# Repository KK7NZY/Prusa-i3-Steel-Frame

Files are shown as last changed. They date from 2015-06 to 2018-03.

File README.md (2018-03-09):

P3Steel
---
RepRap P3Steel parts and build instructions.

### Bill of Materials

**Vitamins**

- (1) [Steel Frame V2.01](http://orballoprinting.com/en/frame/8-prusa-i3-steel-frame-p3steel.html)
- (1) [Steel X-Carriage Kit](https://www.ebay.com/itm/P3Steel-Lasercut-All-metal-kit-for-v2-v2-5-v4-Frame-Prusa-i3-3D-Printer-RepRap/142481311508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)

**Proteins**

- (2) psu-clamp-top.stl
- (2) psu-clip.stl
- (1) psu-clamp-bottom.stl
- (2) endstop-holder.stl
- (1) feet-dampner-set.stl
- (1) y-belt-holder.stl
- (1) y-endstop.stl
- (1) ir-sensor-mount.stl

**Electronics**

- (1) [Azteeg X5 mini v1.1](https://www.panucatt.com/azteeg_X5_mini_reprap_3d_printer_controller_p/ax5mini.htm)
- (1) 12v/30a DC Universal Regulated Switching Power Supply 360w
- (1) 9 ft. 14/3 Power Tool Replacement Cord
- (1) [All-metal E3D v6 Hotend - 12 Volt / 1.75mm Universal](https://www.filastruder.com/products/all-metal-e3d-v6-hotend)
- (1) 12V 220W Silicone Heater w/adhesive tape (200mm x 200mm)
- (1) [Mini Differential IR Height Sensor](https://www.filastruder.com/collections/electronics/products/mini-differential-ir-height-sensor)

**Hardware**

- (2) 8mm x 320mm Precision Chromed Linear Shaft Rod
- (2) 300mm x 8mm Lead 4 Start Lead Screw & Nut
- (2) 8mm x 406mm Precision Chromed Linear Shaft Rod
- (4) Heated Bed Adjustment M3 Thumb Nut
- (1) MK8 Filament all-Metal Remote Bowden Extruder Parts
- (1) Aluminum Spacer (6 x 1/4" x 3/8")
- (3) Mechanical Endstop Switch
- (1) Aluminum Bed Build Plate (200mm x 200mm x 2mm)
- (1) Heated Bed Tempered Borosilicate Glass Plate

**Mechanical parts**

- (4) LM8UU Linear Bearings 
- (7) Igus DryLin® RJ4JP 01-08
- (2) 5mm to 8mm Shaft Rigid Motor Wheel Coupling Coupler 
- (1) GT2 2mm pitch 6mm wide Timing Belt (5 Meters)
- (2) GT2 Pulley 16T 6mm Width
- (2) 608 Ball Bearing
- (4) [NEMA 17 Stepper Motor](https://www.lulzbot.com/store/parts/nema-17-stepper-motor)
- (1) [Half Height NEMA 17 Stepper Motor](https://www.lulzbot.com/store/parts/half-height-nema-17-stepper-motor)
- (30) [Female Crimp terminal for 0.1" pitch headers](https://mod-one.com/female-crimp-terminal-for-0-1-pitch-headers-5-pack/)
- (5) Dupont 2.54mm Connector Housing Female

**Optional**

- (1) [Mellow-Yellow MDPC-X Sleeve (25ft)](https://mod-one.com/mdpc-x-cable-sleeve/)

### Temperature Control

http://smoothieware.org/temperaturecontrol?s[]=temperaturecontrol&s[]=pid&s[]=autotuning#pid-autotuning

**PID Settings**

```sh
# E3D-v6 Hotend
M303 E0 S230 C10
// Cycle 4: max 236.676,min:225.84,avg seperation: 0.281876
   Ku: 59.9243,Pu 35.25
   Kp: 36.0
   Ki: 2.040
   Kd: 158

# Heatbed
M303 E1 S50 C8
// Cycle 4: max: 50.6263, min: 49.3329, avg separation: 0.00749207
   Ku: 502.053, Pu: 52.1
   Trying:
   Kp: 301.2
   Ki: 11.564
   Kd:  1962
```

### Resources:
- [P3Steel Wiki](http://reprap.org/wiki/P3Steel)
- [Triffid Hunter's Calibration Guide](http://reprap.org/wiki/Triffid_Hunter's_Calibration_Guide)
- [Prusa Calculator](http://www.prusaprinters.org/calculator/)
- [Prusa3D Slic3r](https://github.com/prusa3d/Slic3r)
- [RepRap GCode Cheat Sheet](https://thingiverse-production-new.s3.amazonaws.com/assets/87/b0/2c/f5/4c/CheatSheet.pdf)
- [Mini height sensor board](https://miscsolutions.wordpress.com/mini-height-sensor-board/)
- [Smoothie Firmware](https://github.com/Smoothieware/Smoothieware/tree/edge/FirmwareBin)
- [E3D-v6_Assembly](https://wiki.e3d-online.com/wiki/E3D-v6_Assembly)
- [Smoothieware Z-probe](http://smoothieware.org/zprobe#configuration-options4)

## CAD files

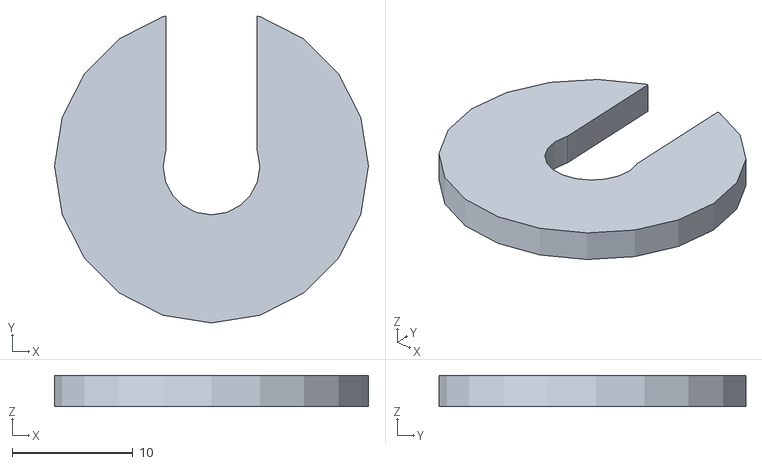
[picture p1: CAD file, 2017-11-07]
proteins/608-bar-spacer.stl
26.0 x 25.4 x 2.60

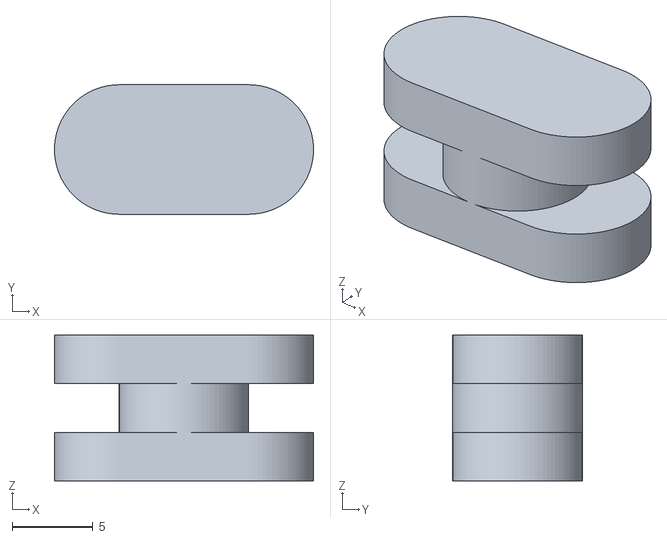
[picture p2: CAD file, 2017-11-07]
proteins/psu-clip.stl
16.0 x 8.00 x 9.00

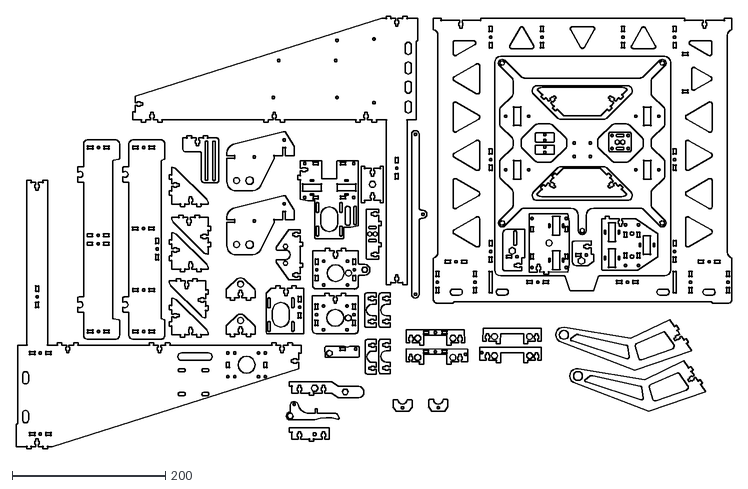
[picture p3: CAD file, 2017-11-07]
vitamins/frame/V1.2-cordobesa-remix/CORDOBESA.dxf
935.1 x 565.2

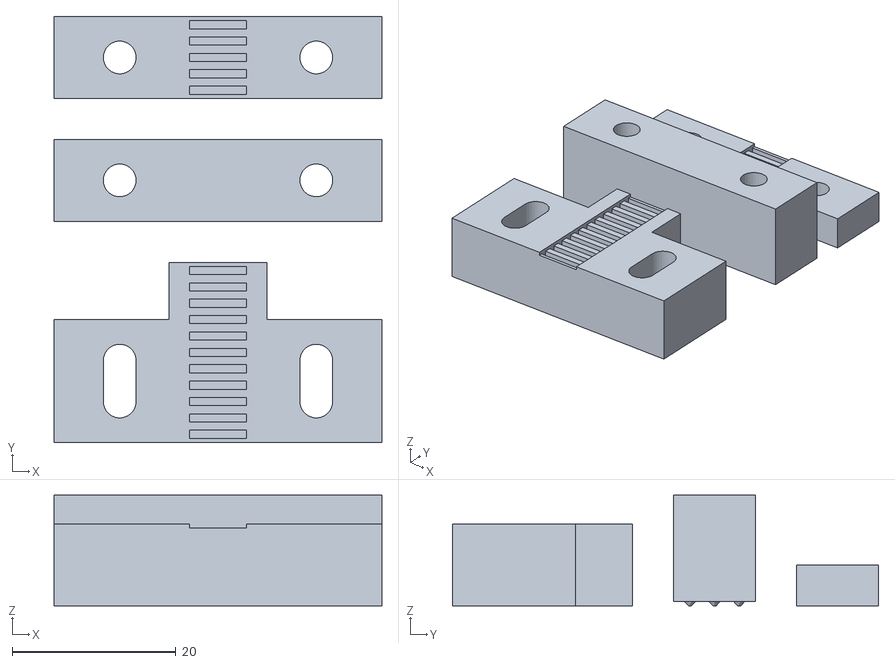
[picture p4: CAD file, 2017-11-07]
proteins/y-belt-holder.stl
40.0 x 52.0 x 13.5

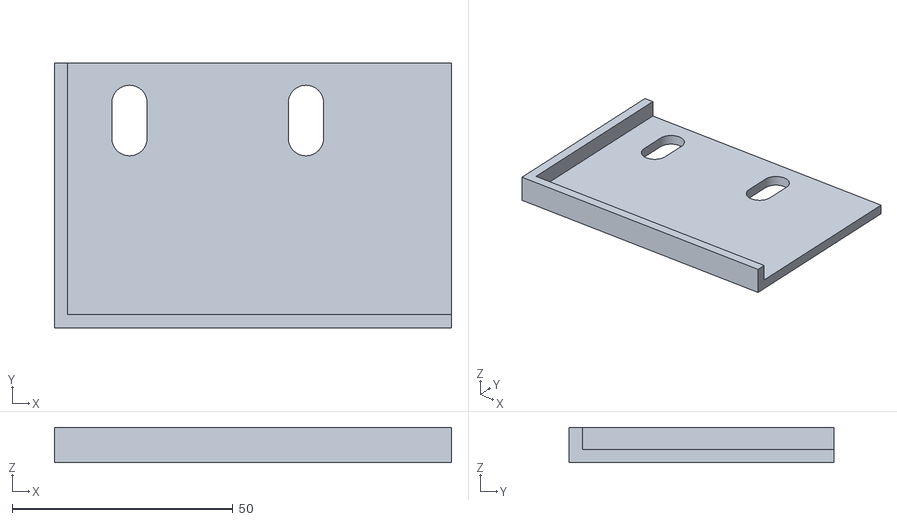
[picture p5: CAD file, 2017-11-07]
proteins/psu-clamp-bottom.stl
90.0 x 60.0 x 8.00

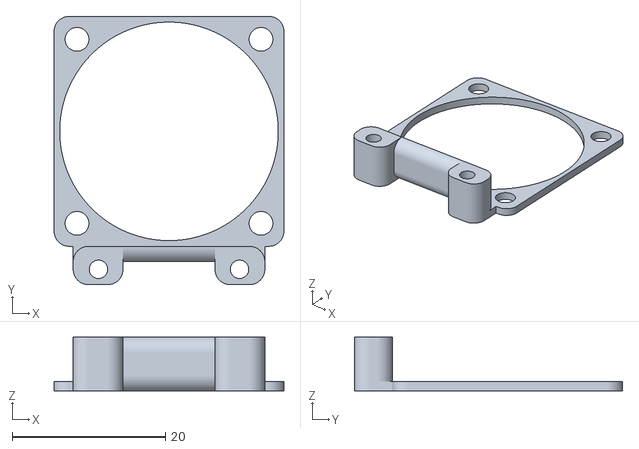
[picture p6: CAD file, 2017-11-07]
proteins/ir-sensor-mount.stl
30.0 x 35.0 x 7.00

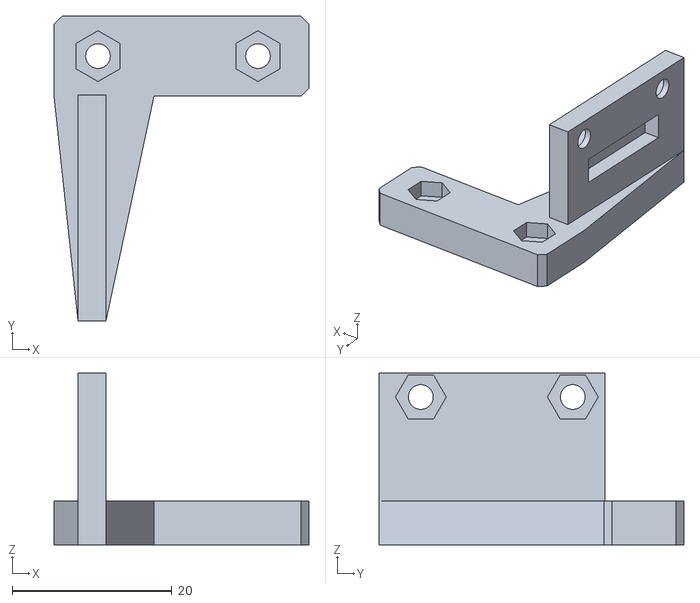
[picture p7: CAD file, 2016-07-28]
proteins/y-endstop.stl
31.9 x 38.1 x 21.5

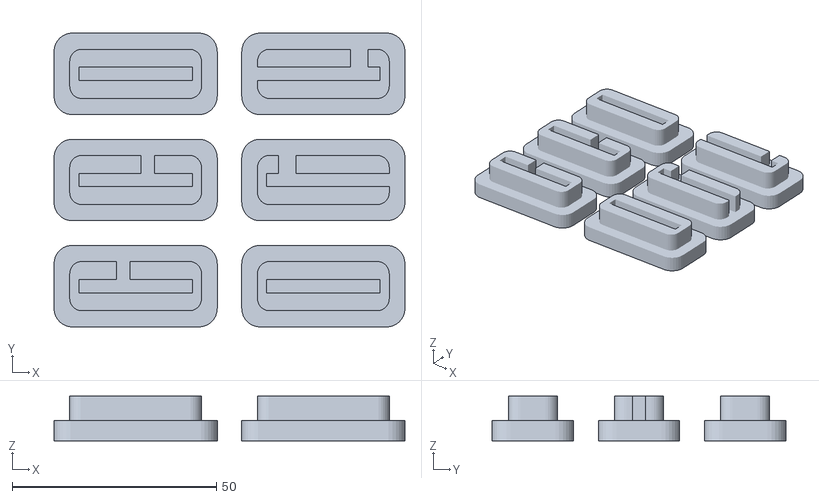
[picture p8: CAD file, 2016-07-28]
proteins/feet-dampner-set.stl
86.0 x 72.0 x 11.0

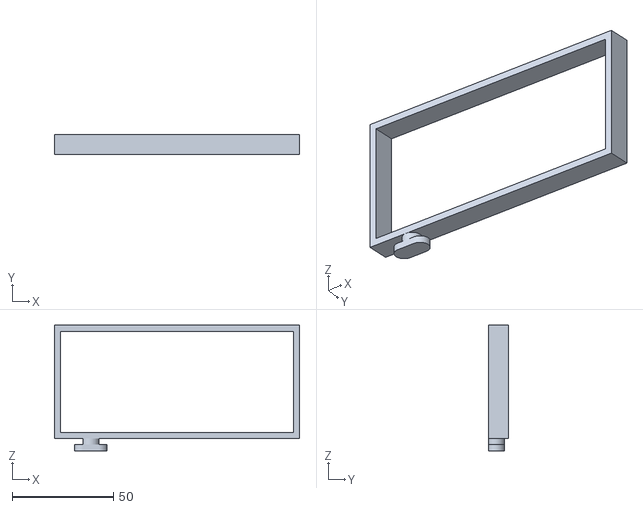
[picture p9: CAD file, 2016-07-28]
proteins/psu-clamp-top.stl
121.0 x 10.00 x 62.0

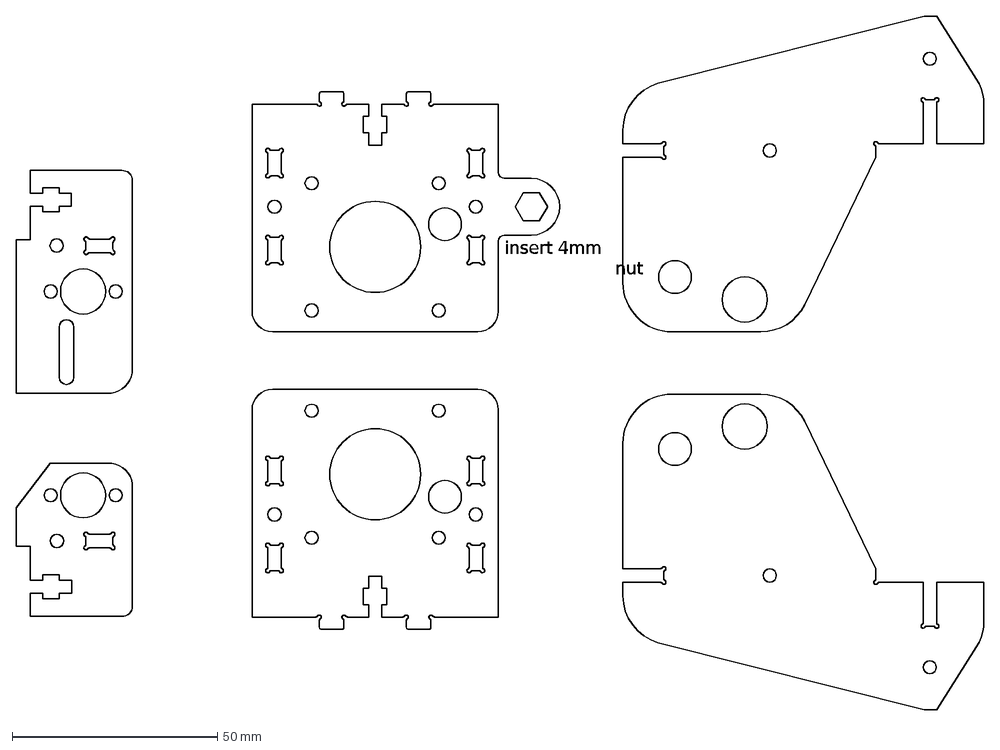
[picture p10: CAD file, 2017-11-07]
vitamins/frame/V1.2-cordobesa-remix/Lead_screw_replacement_parts.dxf
insert 4mm nut

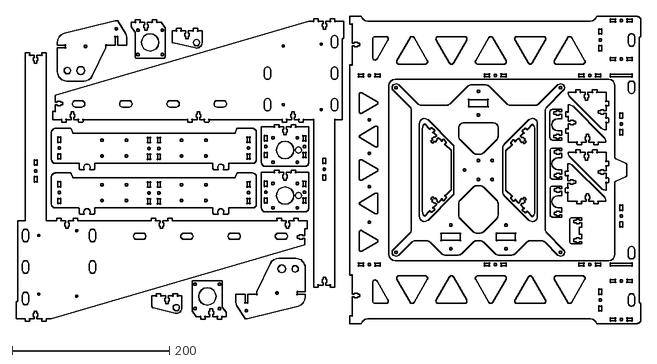
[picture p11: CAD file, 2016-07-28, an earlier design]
vitamins/frame/V1.2/PRUSA_i3_steel_3mm_lasercut_1.2_irobri.dxf
793.6 x 390.0

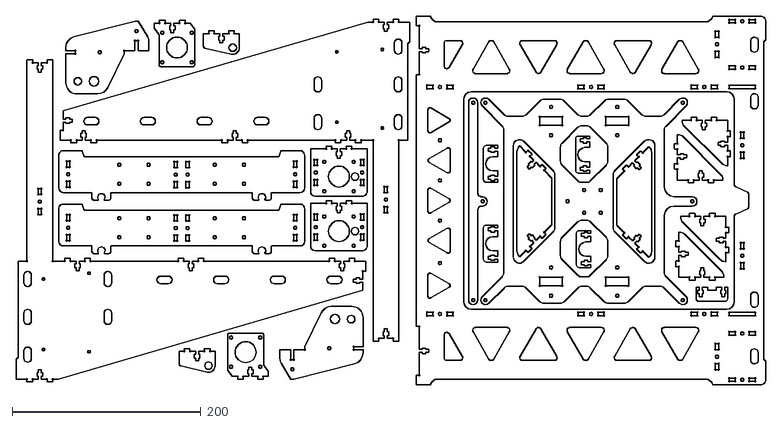
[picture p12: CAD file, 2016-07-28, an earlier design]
vitamins/frame/V2.0/PRUSA_i3_steel_3mm_lasercut_2.0_irobri.dxf
793.6 x 390.0

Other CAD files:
vitamins/frame/V2.5/PRUSA_i3_steel_3mm_lasercut_2.5DXL_e_irobri_V2.dwg
vitamins/frame/V2.1/PRUSA_i3_steel_3mm_lasercut_2.01d_irobri.dwg
vitamins/frame/V1.2-cordobesa-remix/Lead_screw_replacement_parts.dwg
vitamins/frame/V1.2/PRUSA_i3_steel_3mm_lasercut_1.2_irobri.dwg
vitamins/frame/V2.0/PRUSA_i3_steel_3mm_lasercut_2.0_irobri.dwg

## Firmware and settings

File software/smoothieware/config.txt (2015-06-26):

# Robot module configurations : general handling of movement G-codes and slicing into moves
default_feed_rate                            4000             # Default rate ( mm/minute ) for G1/G2/G3 moves
default_seek_rate                            4000             # Default rate ( mm/minute ) for G0 moves
mm_per_arc_segment                           0.5              # Arcs are cut into segments ( lines ), this is the length for these segments.  Smaller values mean more resolution, higher values mean faster computation
#mm_per_line_segment                          5                # Lines can be cut into segments ( not usefull with cartesian coordinates robots ).

# Arm solution configuration : Cartesian robot. Translates mm positions into stepper positions
alpha_steps_per_mm                           80               # Steps per mm for alpha stepper
beta_steps_per_mm                            80               # Steps per mm for beta stepper
gamma_steps_per_mm                           1637.7953        # Steps per mm for gamma stepper

# Planner module configuration : Look-ahead and acceleration configuration
planner_queue_size                           32               # DO NOT CHANGE THIS UNLESS YOU KNOW EXACTLY WHAT YOUR ARE DOING
acceleration                                 3000             # Acceleration in mm/second/second.
#z_acceleration                              500              # Acceleration for Z only moves in mm/s^2, 0 disables it, disabled by default. DO NOT SET ON A DELTA
acceleration_ticks_per_second                1000             # Number of times per second the speed is updated
junction_deviation                           0.05             # Similar to the old "max_jerk", in millimeters, see : https://github.com/grbl/grbl/blob/master/planner.c#L409
                                                              # and https://github.com/grbl/grbl/wiki/Configuring-Grbl-v0.8 . Lower values mean being more careful, higher values means being faster and have more jerk

# Stepper module configuration
microseconds_per_step_pulse                  1                # Duration of step pulses to stepper drivers, in microseconds
base_stepping_frequency                      100000           # Base frequency for stepping

# Stepper module pins ( ports, and pin numbers, appending "!" to the number will invert a pin )
alpha_step_pin                               2.1              # Pin for alpha stepper step signal
alpha_dir_pin                                0.11             # Pin for alpha stepper direction
alpha_en_pin                                 0.10             # Pin for alpha enable pin
alpha_current                                1.0              # X stepper motor current
x_axis_max_speed                             30000            # mm/min
alpha_max_rate                               30000.0          # mm/min actuator max speed

beta_step_pin                                2.2              # Pin for beta stepper step signal
beta_dir_pin                                 0.20             # Pin for beta stepper direction
beta_en_pin                                  0.19             # Pin for beta enable
beta_current                                 1.0              # Y stepper motor current
y_axis_max_speed                             30000            # mm/min
beta_max_rate                                30000.0          # mm/min actuator max speed

gamma_step_pin                               2.3              # Pin for gamma stepper step signal
gamma_dir_pin                                0.22             # Pin for gamma stepper direction
gamma_en_pin                                 0.21             # Pin for gamma enable
gamma_current                                1.0              # Z stepper motor current
z_axis_max_speed                             300              # mm/min
gamma_max_rate                               300.0            # mm/min actuator max speed

# Serial communications configuration ( baud rate default to 9600 if undefined )
uart0.baud_rate                              115200           # Baud rate for the default hardware serial port
second_usb_serial_enable                     false            # This enables a second usb serial port (to have both pronterface and a terminal connected)
#msd_disable                                 false            # disable the MSD (USB SDCARD) when set to true

# Extruder module configuration
extruder_module_enable                       true             # Whether to activate the extruder module at all. All configuration is ignored if false
extruder_steps_per_mm                        140              # Steps per mm for extruder stepper
extruder_default_feed_rate                   600              # Default rate ( mm/minute ) for moves where only the extruder moves
extruder_acceleration                        500              # Acceleration in mm/sec^2, only used for retracts
extruder_max_speed                           1000             # mm/sec NOTE only used for retracts

extruder_step_pin                            2.0              # Pin for extruder step signal
extruder_dir_pin                             0.5              # Pin for extruder dir signal
extruder_en_pin                              0.4              # Pin for extruder enable signal
delta_current                                1.0              # Extruder stepper motor current

# Laser module configuration
laser_module_enable                          false            # Whether to activate the laser module at all. All configuration is ignored if false.
#laser_module_pin                             2.7              # this pin will be PWMed to control the laser
#laser_module_max_power                       0.8              # this is the maximum duty cycle that will be applied to the laser
#laser_module_tickle_power                    0.0              # this duty cycle will be used for travel moves to keep the laser active without actually burning

# Hotend temperature control configuration
temperature_control.hotend.enable            true             # Whether to activate this ( "hotend" ) module at all. All configuration is ignored if false.
temperature_control.hotend.thermistor_pin    0.24             # Pin for the thermistor to read
temperature_control.hotend.heater_pin        2.5              # Pin that controls the heater
temperature_control.hotend.thermistor        EPCOS100K        # see http://smoothieware.org/temperaturecontrol#toc5
#temperature_control.hotend.beta             4066             # or set the beta value

temperature_control.hotend.set_m_code        104              #
temperature_control.hotend.set_and_wait_m_code 109            #
temperature_control.hotend.designator        T                #

temperature_control.hotend.p_factor          13.7             #
temperature_control.hotend.i_factor          0.097            #
temperature_control.hotend.d_factor          24               #

temperature_control.bed.enable               false            #
temperature_control.bed.thermistor_pin       0.23             #
temperature_control.bed.heater_pin           2.7              #
temperature_control.bed.thermistor           Honeywell100K    # see http://smoothieware.org/temperaturecontrol#toc5
#temperature_control.bed.beta                4066             # or set the beta value

temperature_control.bed.set_m_code           140              #
temperature_control.bed.set_and_wait_m_code  190              #
temperature_control.bed.designator           B                #

# Switch module for fan control
switch.fan.enable                            true             #
switch.fan.input_on_command                  M106             #
switch.fan.input_off_command                 M107             #
switch.fan.output_pin                        2.4              #

switch.misc.enable                           false            #
switch.misc.input_on_command                 M42              #
switch.misc.input_off_command                M43              #
switch.misc.output_pin                       2.4              #

# automatically toggle a switch at a specified temperature. Different ones of these may be defined to monitor different temperatures and switch different swithxes
# useful to turn on a fan or water pump to cool the hotend
#temperatureswitch.hotend.enable                true             #
#temperatureswitch.hotend.designator          T                # first character of the temperature control designator to use as the temperature sensor to monitor
#temperatureswitch.hotend.switch              misc             # select which switch to use, matches the name of the defined switch
#temperatureswitch.hotend.threshold_temp      60.0             # temperature to turn on (if rising) or off the switch
#temperatureswitch.hotend.heatup_poll         15               # poll heatup at 15 sec intervals
#temperatureswitch.hotend.cooldown_poll       60               # poll cooldown at 60 sec intervals
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

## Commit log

2015-05-26 Added Createc 3D x-end motor and idler.
    [x-end-idler-B.stl, x-end-motor.stl, x-end_Idler-A.stl]
2015-05-26 Renamed idler.
    [x-end_Idler-A.stl]
2015-05-27 Added Sampaino's x motor and idler ends.
    [x-carriage.stl, x-end-idler-A.stl, x-end-idler-B.stl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]
2015-05-29 Added Y motor spacer by Psych0o.http://www.thingiverse.com/thing:525851
    [y-motor-spacer.stl]
2015-05-29 Added P3Steel lasercut version 2.01. http://www.thingiverse.com/thing:576456
    [PRUSA_i3_steel_3mm_lasercut_2.01d_irobri.dwg, PRUSA_i3_steel_3mm_lasercut_2.01d_irobri.dxf]
2015-05-31 Added P3Steel Improved X-axis Printed Parts Collection. http://www.thingiverse.com/thing:607891
    [knurled-nut-knob.stl, pulley-623ZZ.stl, x-carriage-rework.stl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]
2015-06-02 Renamed files.
    [x-belt-pulley-623ZZ.stl, x-belt-tensioner-knob.stl, x-belt-tensioner.stl]
2015-06-02 Added E3D v6 Bowden X-carriage mount Prusa i3. http://www.thingiverse.com/thing:547706
    [bowden-carriage-clamp-50mmFanbracket.stl, bowden-carriage-clamp-FanMount.stl, bowden-carriage-clamp.stl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]
2015-06-06 Removed bowden carriage clamp with fan mounts.
    [bowden-carriage-50mmFanBracket.stl, bowden-carriage-clamp-FanMount.stl, bowden-carriage-clamp.stl]
2015-06-07 Added bowden extruder, and extra proteins.
    [bowden-carriage-50mmFanBracket.stl, bowden-carriage-clamp.stl, bowden-carriage.stl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]
2015-06-07 Added http://www.thingiverse.com/thing:456602
    [bowden-intake-duct-30mm.stl]
2015-06-08 Added airtripper filament driver mount for E3D ver6. http://www.thingiverse.com/thing:868212
    [filament-driver.stl]
2015-06-08 Added extruder driver body. http://www.thingiverse.com/thing:731585
    [filament-driver.stl]
2015-06-08 Added X Carriage rework type without ties. http://www.thingiverse.com/thing:651517
    [x-carriage-rework.stl]
2015-06-08 Added http://www.thingiverse.com/thing:532424
    [vibration-dampening-feet-back.stl, vibration-dampening-feet-front.stl]
2015-06-09 Added http://www.thingiverse.com/thing:592637
    [vibration-dampening-feet-middle.stl]
2015-06-09 Added http://www.thingiverse.com/thing:868212
    [airtripper-bowden-body.stl]
2015-06-09 Added http://www.thingiverse.com/thing:487891
    [airtripper-bowden-idler.stl]
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2015-06-11 Added remixed power supply cover. http://www.thingiverse.com/thing:876601
    [psu-cover.stl]
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2015-06-26 Added azteeg x5 mini firmware and sample config.
    [config.txt]
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2015-06-27 Added bill of materials.
    [bill-of-materials.xlsx]
2015-06-27 Modified bill of materials.
    [BOM.xlsx]
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2015-07-06 Added simple filament spool stand v3.2 http://www.thingiverse.com/thing:296971
    [spool-stand-bar.stl, spool-stand-side.stl]
2015-07-07 Added spool stand. http://www.thingiverse.com/thing:654312
    [spool-stand.stl]
2015-07-12 Added endstop for x, and z. Possibly can also use for y. http://www.thingiverse.com/thing:64254
    [compact-endstop.stl]
2015-07-14 Updated configuration. Had issue with homing z axis. Solution is to slow down the homing rate.
2015-07-14 Added compact mechanical endstop holder for x, and z axis. http://www.thingiverse.com/thing:28728
    [xz-endstop.stl]
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2015-07-19 Updated BOM and slicer config.
    [BOM.xlsx]
2015-07-19 Had problems with z-axis during print. To fix needed to change wiring, set z home to min, and uncomment z-axis acceleration.
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2015-07-25 Updated Build of materials.
    [BOM.xlsx]
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2015-08-16 Added cube calibration print, and update slic3r config.
    [hollow_cube.stl]
2015-11-17 Added calibration cube and updated firmware.bin file.
    [25mm_cube.stl]
2016-01-18 Added e3d carriage remix with proximity mount.
    [BOM.xlsx, e3d-carriage-50mmFanBracket.stl, e3d-carriage-clamp.stl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]
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2016-01-18 Moved extruder parts to proteins directory.
    [airtripper-bowden-axle.stl, airtripper-bowden-body.stl, airtripper-bowden-idler.stl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]
2016-01-18 Removed airtripper files. Many other options now.
    [airtripper-bowden-axle.stl, airtripper-bowden-body.stl, airtripper-bowden-idler.stl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]
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2016-05-21 Added *.dwg frame vitamins
    [PRUSA_i3_steel_3mm_lasercut_1.2_irobri.dwg, PRUSA_i3_steel_3mm_lasercut_1.2_irobri.dxf, PRUSA_i3_steel_3mm_lasercut_2.01d_irobri.dwg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]
2016-05-22 Added initial plastic parts.
    [feet-dampner-set.stl, ramps-offset-base-a.stl, ramps-offset-base-b.stl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]
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2016-07-25 Modified and tested firmware.
    Swapped out the e-steps for bulldog lite setup. Modified PID settings and commented out LCD options.
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2016-07-28 Removed files. Preparing to merge develop.
    [PRUSA_i3_steel_3mm_lasercut_2.01d_irobri.dwg, PRUSA_i3_steel_3mm_lasercut_2.01d_irobri.dxf, e3d-carriage-clamp.stl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]
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2016-10-18 Added marling firmware config.
    [Configuration.h]
2016-10-30 Add files via upload
    http://www.thingiverse.com/thing:341091
    [hex-shroud.stl]
2017-02-07 Update Configuration.h
    Upgraded to Marlin 1.0.2
    [Configuration.h]
2017-02-09 M303 E0 S200 C8
    M301 P18.13 I1.07 D76.84
    [Configuration.h]
2017-04-09 Replaced plastic parts with steel, and swapped RAMPs board for smoothie.
    [Configuration.h, bulldog-lite-extruder-mount.stl, hex-shroud.stl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]
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2017-04-23 Inverted extruder direction pin.
    Moved extruder mount to back of printer. Inverted direction pin. http://smoothieware.org/pin-configuration
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2017-05-01 Purchase spacer from home-depot.
    [y-motor-spacer.stl]
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2017-05-07 Added y-belt holder parts. Works better.
    [y-axis-clamps.stl, y-belt-holder.stl, y-belt-tensioner.stl]
2017-05-07 Added missing parts to STL.
    [y-belt-holder.stl]
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2017-05-14 Added ir-sensor-mount thing from http://www.thingiverse.com/thing:1576084/#files
    [ir-sensor-mount.stl]
2017-05-14 Created simple spacer for x-axis bearing. Keeps belt on bearing and prevents bearing from moving.
    [608-bar-spacer.stl]
2017-05-16 Add files via upload
    This is mounted to the x -axis carriage. Use if using the same end-stop holder.
    [x-endstop-bumber.stl]
2017-05-16 fixed spelling.
    [x-endstop-bumper.stl]
2017-05-20 endstop-holder didn't work well. Trying other alternatives.
    [endstop-holder.stl]
2018-03-10 Removed unused printed parts
    [bulldog-lite-extruder-shroud.stl, x-endstop-bumper.stl]
